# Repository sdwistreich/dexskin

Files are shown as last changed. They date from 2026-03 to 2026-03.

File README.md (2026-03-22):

# DexSkin (CoRL 2025)

DexSkin Demo

Suzannah Wistreich*, Baiyu Shi*, Stephen Tian*, Samuel Clarke, Michael Nath, Chengyi Xu, Zhenan Bao, Jiajun Wu  
Stanford University, UAB · CoRL 2025  

🔗 Project page: https://dex-skin.github.io

## 🎉 Open-Source Release: DexSkin — High-Coverage Conformable Robotic Skin for Contact-Rich Manipulation

We are excited to release **DexSkin**! 🎊  

DexSkin is a soft, high-resolution, conformable tactile sensing system designed for **contact-rich robotic manipulation**. It enables dense, localized sensing across complex surfaces and supports learning-based control in real-world settings.

---
## Getting Started

**This repository contains the full stack needed to:**

- **Fabricate the DexSkin sensor** → [hardware/README.md](hardware/README.md)  
- **Set up + interface with the hardware** → [firmware/README.md](firmware/README.md)  
- **Integrate DexSkin with learning pipelines** → [learning/README.md](learning/README.md)  

---

## Repository Overview

```
hardware/
  ├── finger/          # electrode design, finger assembly
  ├── fpcb/            # PCB interconnects
  ├── calibration/     # pneumatic calibration setup (STLs)
  └── readout_pcb/     # readout board Gerbers

firmware/    
  ├── dexskin_finger_firmware.bin       # ESP32 flashing binaries
  └── scripts/                          # readout and visualization scripts

learning/
  └── scripts/        # RL integration example
```
---

## BibTeX

If you found this open-source helpful, please consider citing:
```
@inproceedings{wistreich2025dexskin,
    title={DexSkin: High-Coverage Conformable Robotic Skin for Learning Contact-Rich Manipulation},
    author={Suzannah Wistreich and Baiyu Shi and Stephen Tian and Samuel Clarke and Michael Nath and Chengyi Xu and Zhenan Bao and Jiajun Wu},
    booktitle={Conference on Robot Learning (CoRL)},
    year={2025},
    eprint={2509.18830},
    archivePrefix={arXiv},
    primaryClass={cs.RO},
    url={https://arxiv.org/abs/2509.18830},
}
```

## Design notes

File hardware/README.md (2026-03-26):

# Hardware & Assembly Instructions

This folder contains DexSkin hardware assets for fabricating the sensor, ordering the PCBs, and reproducing the calibration setup described in the paper.

## Release Status

Currently available in this folder:

- Finger electrode SVG layout
- Flexible PCB manufacturing files for the sensor array interconnects
- Readout PCB Gerbers
- Calibration fixture STLs

In progress (target: mid-April 2026):

- Readout board BOM
- Calibration fabrication guide
- Assembly and ordering recommendations

## Folder Guide

### `finger/`

- `DexSkin_Electrode_design.svg`: Layout of top and bottom capacitive electrode layers for the finger design described in the paper
  - *For researchers interested in access to the stretchable cylindrical DexSkin form described in the paper or tactile arrays in other grid formats, please contact Baiyu Shi at the Bao Group (`baiyushi@stanford.edu`) regarding sample availability.*

### `fpcb/`

- `dexskin_5pin_row_interconnection.zip` and `dexskin_12pin_column_interconnection.zip`: flexible PCB interconnect files for the stretchable cylindrical DexSkin embodiment described in the paper.
- `5pin_row_fabrication_output.zip` and `12pin_column_fabrication_output.zip`: fabrication-ready Gerber packages for the 5 x 12 taxel flexible sensor layout for easy adoption.
- 5 x 12 taxel layout, mountable on flat or cylindrical grippers
- 2.5 mm x 2.5 mm square taxels
- 1.5 mm spacing between neighboring taxels

Special flex-PCB ordering notes:

- These fabrication-output Gerbers include a few layer specifications that should be communicated explicitly to the flex-PCB vendor during ordering
- **Mechanical Layer 1**: PCB outline
- **Top Overlay**: top EMI shielding film outline
- **Bottom Overlay**: bottom stiffener outline

### `readout_pcb/`

- `dexskin_readout_pcb_v1.1.zip`: Manufacturing files for the 4-layer readout board used to read both finger arrays simultaneously, prepared as a fabrication-ready Gerber archive

### `calibration/`

- `Final_Mold_Top.stl` 
- `Final_Mold_Bot.stl` 
- `Final_Mold_Supporting_Platform.stl` 
- `D20.8_Inner_Sleeve_TOP.stl`
- `D20.8_Inner_Sleeve_BOT.stl`
    - 3D-printable parts used to mold the Ecoflex and build airtight chambers for the 3-minute transfer calibration procedure described in the paper.

## Assembly Guide
Assembly overview:

DexSkin Demo

For a full walkthrough, please see the [assembly video](https://dex-skin.github.io/open_source.html#assembly-guide) on our project website!

**Materials**
- Two fabricated fPCB pieces
- Thin double-sided tape
- Nonconductive dielectric layer
- Sharp scalpel for trimming dielectric and tape
  
In our builds, we use a sandpaper-structured midlayer as the dielectric.

**Procedure**
1. **Prepare base layer**:
   
     Apply double-sided tape along the boundary of one fPCB piece.
2. **Attach dielectric**:

     Laminate the dielectric layer onto the second fPCB piece, trimming as needed.
3. **Align electrodes**:

     Carefully align the top and bottom electrode layers by matching the exposed copper taxels.
4. **Bond Assembly**:

     Press around the edges to ensure the double-sided tape bonds the two pieces together securely.

After assembly, verify the sensor by following the firmware instructions provided in [`../firmware/README.md`](../firmware/README.md). Then, run:
- [`../firmware/scripts/readout.py`](../firmware/scripts/readout.py)
- [`../firmware/scripts/visualize.py`](../firmware/scripts/visualize.py)

to verify that the sensor reads out correctly and view the real-time visualization:

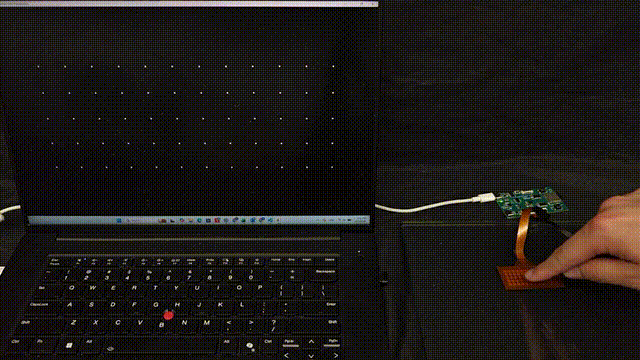
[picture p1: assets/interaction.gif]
DexSkin Demo


## Manufacturing Notes

- The ZIP archives in `fpcb/` and `readout_pcb/` are intended for direct submission to a PCB manufacturer.
- If your manufacturer asks for layer clarification on the flexible PCB files, you may use the layer notes above.

## Planned Additions

- Readout PCB BOM, including alternative parts where distributor availability changes
- Calibration fixture build notes
- Step-by-step assembly guidance

Last updated: March 26, 2026

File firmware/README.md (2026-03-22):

# DexSkin Interfacing Setup Guide

This guide explains:
- [DexSkin firmware setup](#firmware-setup)
- [Board readout and visualization scripts](#readout--visualization-setup)

Compatible with **Windows, macOS, and Linux**

---
## Firmware Setup

### 1. Install FTDI Drivers

If you haven’t worked with embedded systems before, you will need a driver to communicate with the onboard Serial USB. Please visit and install the USB serial drivers:

https://ftdichip.com/drivers/vcp-drivers/

- Select your OS and install
- **Linux:** typically already installed (check via Step #3)

---

### 2. Install Flashing Tool (esptool)

The esptool utility is a universal Python-based application used to communicate and flash in firmware with the ESP32 MCU series.

    pip install esptool

---

### 3. Identify Serial Port

Connect the board via USB-C.

If there are two ports, orient the board such that ESP32 is facing up, antenna is on the right, and the use **top-left port**.

You need to identify the specific port and its name assigned to the connected board:

**Windows**

Right-click the Start menu, select Device Manager, and expand Ports (COM & LPT). Look for USB Serial Port (`COMx`).

**macOS**

    ls /dev/cu.usbserial*

**Linux**

    ls /dev/ttyUSB*

---

### 4. Flash Firmware

Download the provided [`dexskin_finger_firmware.bin`](../firmware/dexskin_finger_firmware.bin). Navigate to the firmware directory and run:

    esptool --chip esp32s3 --port PORT --baud 460800 write_flash 0x0 dexskin_finger_firmware.bin

Replace `PORT` with your device found in Step #3.

**Example (macOS):**

    esptool --chip esp32s3 --port /dev/cu.usbserial-DP05L1VU --baud 460800 write_flash 0x0 dexskin_finger_firmware.bin

---

### 5. Troubleshooting

**Automatic Boot:**  
The board should enter flashing mode automatically once the flash command is executed.

**If “Failed to connect”:**
1. Hold **User/Boot** on the top right of the board.
2. Press + release **Reset** on the bottom right of the board.
3. Release **User/Boot** button before retrying flash command.
4. Retry flash command.

---

### 6. Completion

When the terminal displays

    Hard resetting via RTS pin…

the firmware update is complete.

You may need to press the **Reset** button once more to cleanly power cycle and boot up the system.

---

## Board Readout & Visualization Scripts

### Python Dependencies

We provide two Python scripts for interfacing and visualization DexSkin sensor readings.  
Tested with Python 3.10 (Python ≥ 3.8 supported).

**Required packages:**
- PyQt5 (5.15.11)
- pyqtgraph (0.13.7)
- pyserial (3.5)
- numpy (2.0.2)

**Quick Setup (conda example):**

    conda create -n dexskin_env python=3.10 -y
    conda activate dexskin_env
    pip install PyQt5==5.15.11 pyqtgraph==0.13.7 pyserial==3.5 numpy==2.0.2

---

### Script Overview

The software architecture is split into two independent processes that communicate via shared memory. This allows the readout script to run at high priority for data logging, while the visualization script consumes data for display without slowing down sensor sampling.

- **[`./scripts/readout.py`](./scripts/readout.py)**: Handles serial communication, packet decoding, and baseline normalization. **Always run this script first**, it must be running for the visualization or any other application to access sensor data.

- **[`./scripts/visualize.py`](./scripts/visualize.py)**: Provides a real-time visualization of tactile data for both the left and right fingers. Each taxel is displayed as a white dot, with dot size proportional to the raw sensor values (sampled pressure / force magnitude). If the script is running correctly, the visualization will look like:

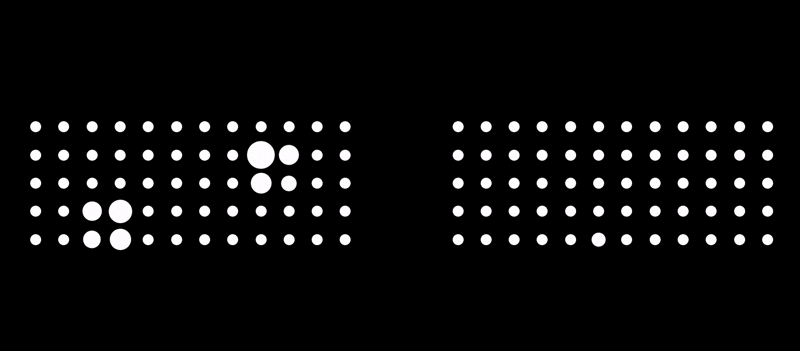
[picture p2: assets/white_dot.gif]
DexSkin Demo


---

### Developer Guide: Interfacing with Shared Memory

The DexSkin system exposes its real-time data buffer to the operating system’s shared memory. This allows developers to write their own scripts (e.g., for Machine Learning inference, ROS robot control, or custom logging) without modifying the core driver.

Any Python script running on the same machine can attach to the shared memory block as a client:

    SHM_NAME = 'dexskin_memory'
    NUM_TAXELS = 120

    try:
        self.shm = shm.SharedMemory(name=SHM_NAME)
        self.frame_buffer = np.ndarray((NUM_TAXELS,), dtype=np.float32, buffer=self.shm.buf)
        print(f"Attached to shared memory: {SHM_NAME}")
    except FileNotFoundError:
        print(f"ERROR: Shared memory block '{SHM_NAME}' not found.")
        print("Please ensure the data providing script is running.")
        sys.exit(1)

Then in other function calls, use:

    self.frame_buffer.copy()

to access latest data.

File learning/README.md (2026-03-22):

# DexSkin Learning Guide

This guide gives a brief overview of data collection and base policy training with DexSkin. We also provide several sample scripts for RL fine-tuning with DexSkin.

---

## Data Collection

We collect real-world demonstrations using a teleoperated Franka robot setup equipped with DexSkin sensors.

Each demonstration consists of:
- Robot observations (e.g., proprioception, optional vision via wrist camera)
- DexSkin tactile readings
- Corresponding action trajectories

These demonstrations are used to train policies via imitation learning. In our setup, ~50 human demonstrations per task are sufficient to learn a reasonable base policy.

---

## Base Policy Training

We train a base manipulation policy using a standard **diffusion policy** formulation, though any imitation-learning framework will do.

---

## RL Fine-Tuning with DexSkin

We provide a small set of **example residual RL scripts** to illustrate how DexSkin can be used in real-world, online learning settings. These scripts are provided as a helpful reference implementation. In particular, reward functions, force thresholds, termination conditions, etc. should be adapted to one's own target task and hardware setup.

### Script Overview

- **[`./scripts/franka_env_with_policy.py`](./scripts/franka_env_with_policy.py)**: Defines a Gym-compatible Franka environment that combines a pretrained diffusion policy with a residual controller. The residual action modifies the base policy's gripper action online, where DexSkin signals are used to compute force-threshold rewards together with an action-magnitude penalty.

- **[`./scripts/residual_inference_train_env.py`](./scripts/residual_inference_train_env.py)**: Constructs a `FrankaEnvWithPolicy` environment (from `franka_env_with_policy.py`) and runs Franka rollouts with the base policy plus a residual controller, which is one of:
  - (default) a learned residual policy
  - `--base_policy_only`: the base policy only
  - `--random_residual`: a random residual baseline  

If neither `--base_policy_only` nor `--random_residual` is set, this script can also continue updating the learned residual policy online.

- **[`./scripts/residual_train.py`](./scripts/residual_train.py)**: Trains a residual SAC policy online on the Franka robot. This script loads the pretrained base policy, constructs the DexSkin-enabled `FrankaEnvWithPolicy` environment, performs online rollouts, updates the residual policy, and periodically saves checkpoints.

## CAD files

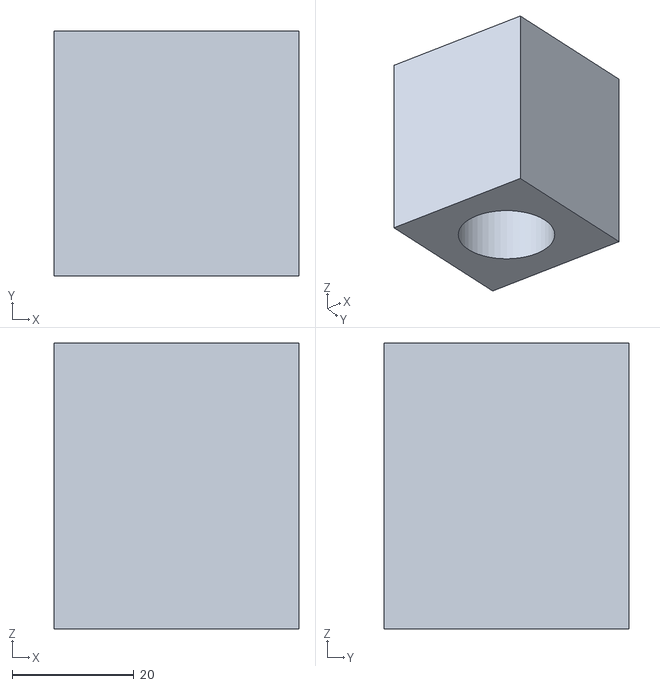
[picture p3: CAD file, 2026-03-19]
hardware/calibration/D20.8_Inner_Sleeve_TOP.stl
40.2 x 40.2 x 47.0

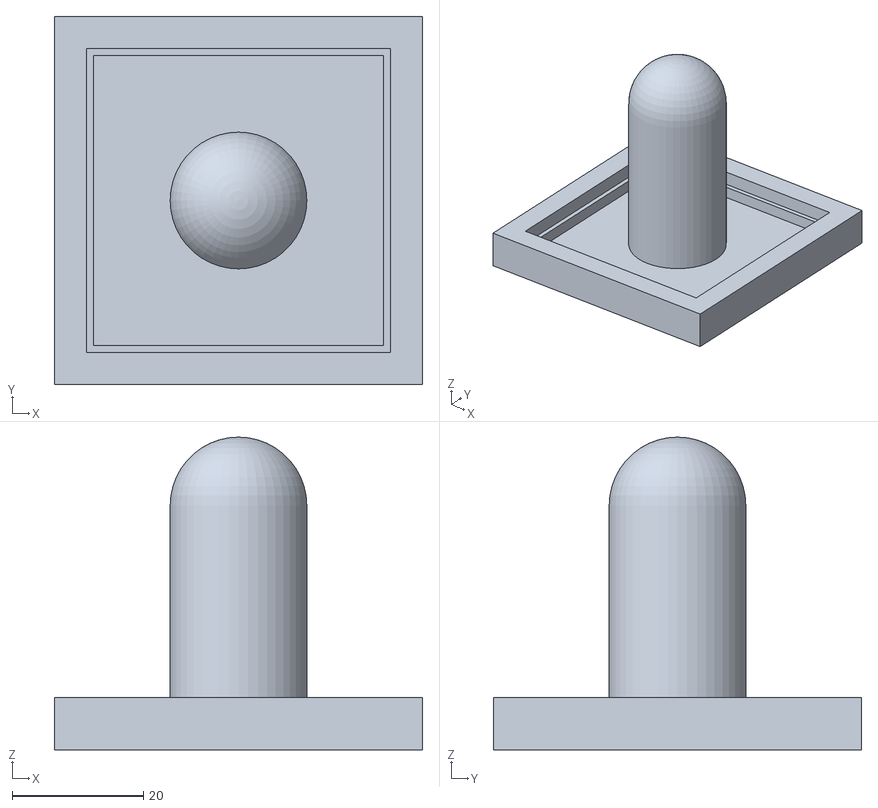
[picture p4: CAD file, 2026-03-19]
hardware/calibration/Final_Mold_Bot.stl
56.0 x 56.0 x 47.6

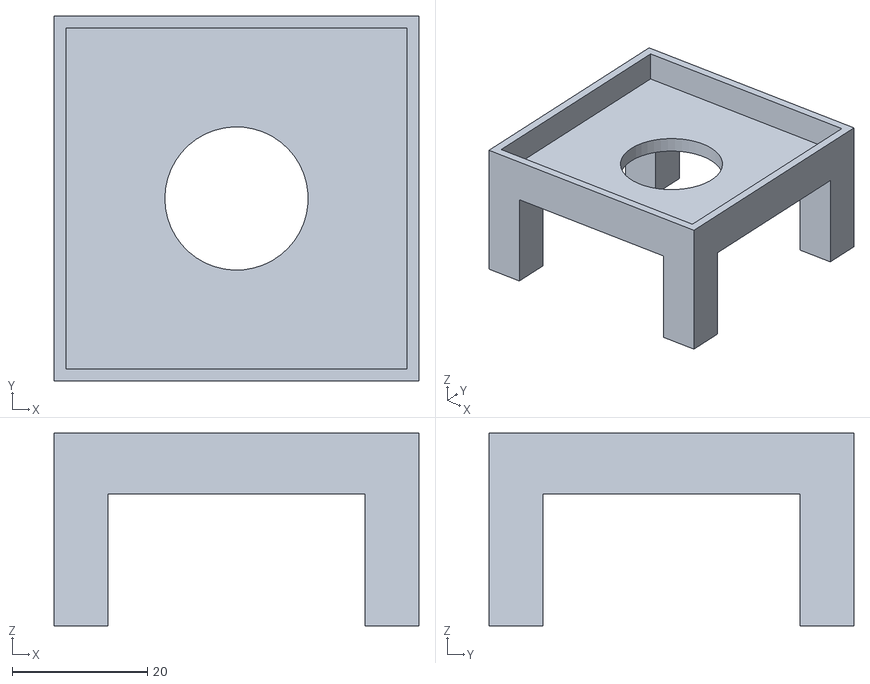
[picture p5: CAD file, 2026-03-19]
hardware/calibration/Final_Mold_Supporting_Platform.stl
54.0 x 54.0 x 28.5

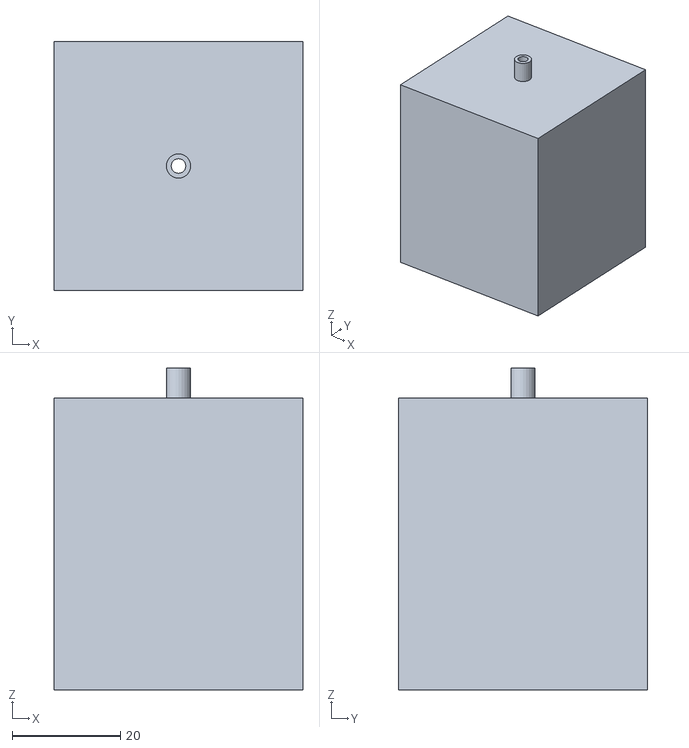
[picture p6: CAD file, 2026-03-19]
hardware/calibration/Final_Mold_Top.stl
46.0 x 46.0 x 59.5

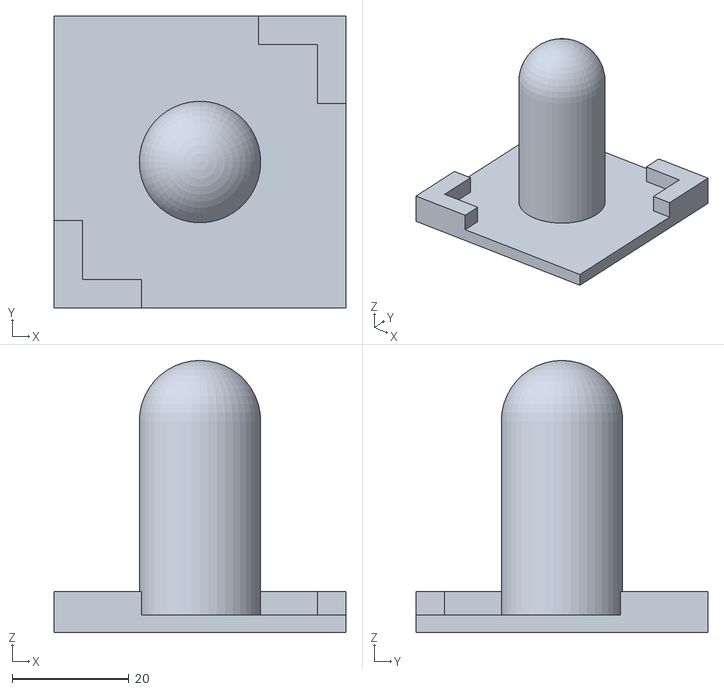
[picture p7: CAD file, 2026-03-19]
hardware/calibration/D20.8_Inner_Sleeve_BOT.stl
50.0 x 50.0 x 46.6

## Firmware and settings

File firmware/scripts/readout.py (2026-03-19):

# File name: readout.py
# Author: Baiyu Shi
# Date created: Jan.2025
# Version: v1.3

import serial
import time
import numpy as np
from multiprocessing.shared_memory import SharedMemory
import threading
from serial import SerialException

#the main parameters to change.
PORT = 'COM3'      
BAUDRATE = 460800         #specify the baud rate, default to 460800 with the provided firmware.
NUM_TAXELS = 120            
numRow = 10
numCol = 12
NUM_TAXELS = numRow * numCol       
BASELINE_SAMPLE_NUM = 30      # Number of frames to be averaged for baselines.
FLUSH_FRAME_COUNT = 50        # Number of initial frames to flush to stabilize readouts.
TIMEOUT = 1            
SHM_NAME = 'dexskin_memory' # Shared memory block name

ITEMSIZE = np.dtype(np.float32).itemsize
BUFSIZE = NUM_TAXELS * ITEMSIZE
try:
    shm = SharedMemory(name=SHM_NAME, create=True, size=BUFSIZE)
    print(f"Created New Shared Memory")
except FileExistsError:
    shm = SharedMemory(name=SHM_NAME, create=False)
    print(f"Attached to Existing Memory '{SHM_NAME}'")
shared_frame = np.ndarray((NUM_TAXELS,), dtype=np.float32, buffer=shm.buf)

class MCUController1DShared:
    def __init__(self):
        self.port = PORT
        self.baudrate = BAUDRATE
        self.timeout = TIMEOUT
        self.serial = None

        #baseline and std instantiation.
        self.CurrentFrame = np.zeros(NUM_TAXELS, dtype=np.float32)
        self.baseline = np.zeros(NUM_TAXELS, dtype=np.float32)
        self.std = np.ones(NUM_TAXELS, dtype=np.int32)

        #for calculating FPS.
        self._frame_count = 0
        self._last_fps_time = time.time()
        self.fps = 0.0
        self.running = False

        try:
            self.connect()
            self.init_flush()
            self.start_periodic_task()
        except SerialException as e:
            print(f"SerialException: {e}")

    def connect(self):
        """Open serial port."""
        self.serial = serial.Serial(self.port, self.baudrate, timeout=self.timeout)
        print(f"Serial connected on {self.port} at {self.baudrate}")

    def init_flush(self):
        """
        Discard FLUSH_FRAME_COUNT number of initial frames, then collect
        BASELINE_SAMPLE_NUM frames to compute per-taxel baseline and std.
        """
        flushed = 0
        while flushed < FLUSH_FRAME_COUNT:
            f = self.read_frame(initial=True)
            if f is not None:
                flushed += 1

        frames = []
        while len(frames) < BASELINE_SAMPLE_NUM:
            f = self.read_frame(initial=True)
            if f is not None:
                frames.append(f)

        arr = np.stack(frames, axis=0)
        # compute mean baseline
        self.baseline = np.mean(arr, axis=0)
        var = np.mean((arr - self.baseline)**2, axis=0)
        float_std = np.sqrt(var)
        self.std = float_std.astype(np.int32)
        self.std[self.std < 1] = 1

        print("Baseline computed:", self.baseline)
        print("Std deviation, expected to be below 1:", self.std)

    def read_frame(self, initial=False):
        if self.serial is None:
            raise Exception("Serial not connected.")

        try:
            line = self.serial.readline()
            raw_values = [
                int(val) for val in line.decode('utf-8').rstrip().split(',')
                if val != ''
            ]

            if len(raw_values) != numRow * numCol:
                return None

            frame = np.array(raw_values, dtype=np.int32)
            if frame.size != NUM_TAXELS:
                return None

            if initial:
                return frame

            # normalize and push to shared memory
            self.CurrentFrame = (frame.astype(np.float32) - self.baseline) / self.baseline
            shared_frame[:] = self.CurrentFrame

            self._frame_count += 1
            self._update_fps()
            return None
        
        
        except Exception as e:
            print(f"Error retrieving frame: {e}")
            return None


    def _update_fps(self):
        now = time.time()
        delta = now - self._last_fps_time
        if delta >= 1.0:
            self.fps = self._frame_count / delta
            self._frame_count = 0
            self._last_fps_time = now

    def get_fps(self):
        return self.fps

    def periodic_task(self):
        self.running = True
        interval = 1 / 120
        while self.running:
            self.read_frame(initial=False)
            time.sleep(interval)

    def start_periodic_task(self):
        t = threading.Thread(target=self.periodic_task, daemon=True)
        t.start()
        self.thread = t
        print(f"Started reader thread")

    def stop(self):
        """
        Stop the thread and clean up shared memory.
        Please call this before exiting.
        """
        self.running = False
        if hasattr(self, 'thread'):
            self.thread.join()
        shm.close()
        try:
            shm.unlink()
        except FileNotFoundError:
            pass
        print("Stopped and cleaned up shared memory.")

    def get_frame(self):
        return self.CurrentFrame

if __name__ == '__main__':
    ctrl = MCUController1DShared()
    try:
        while True:
            print(f"FPS: {ctrl.get_fps():.1f}")
            time.sleep(0.5)
    except KeyboardInterrupt:
        #use Keyboard interrupts to end the thread and safely unlink the memory.
        ctrl.stop()

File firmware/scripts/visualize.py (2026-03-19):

# File name: visualize.py
# Author: Baiyu Shi
# Date last modified: 01/09/2025

import numpy as np
import pyqtgraph as pg
from PyQt5 import QtCore, QtGui, QtWidgets
import sys
import multiprocessing.shared_memory as shm

#parameters.
SHM_NAME = 'dexskin_memory'  # Shared memory block name
NUM_TAXELS = 120             # Total number of taxels (5*12*2)
timerDelay = 33             #33ms updates for 30Hz update.

#parameters defining visualization dot layout.
finger_rows = 5
finger_cols = 12
gap = 4.0

positions = []

#visualization settings
min_val, max_val = 0.05, 1.0
min_dot_size = 10
max_dot_size = 150

# Right finger (positive x) on the right of GUI
for r in range(finger_rows):
    for c in range(finger_cols):
        # x starts from gap/2, y is centered vertically around 0
        x = c + gap / 2.0
        y = r - (finger_rows - 1) / 2.0
        positions.append([x, y])

# Left finger (negative x) on the left of GUI.
for r in range(finger_rows):
    for c in range(finger_cols):
        # x starts from -gap/2 and goes left, creating a mirror image
        x = -(c + gap / 2.0)
        y = r - (finger_rows - 1) / 2.0
        positions.append([x, y])

positions = np.array(positions)
assert len(positions) == NUM_TAXELS, "Position array length must match NUM_TAXELS"


class DualFingerVisualization(QtWidgets.QMainWindow):
    def __init__(self):
        super().__init__()
        self.setWindowTitle('DexSkin Tactile Data Visualization')
        self.resize(800, 600)

        try:
            self.shm = shm.SharedMemory(name=SHM_NAME)
            self.frame_buffer = np.ndarray(
                (NUM_TAXELS,), dtype=np.float32, buffer=self.shm.buf
            )
            print(f"Attached to shared memory: {SHM_NAME}")
        except FileNotFoundError:
            print(f"ERROR: Shared memory block '{SHM_NAME}' not found.")
            print("Please ensure the data providing script is running.")
            sys.exit(1)

        graphicswidget = pg.GraphicsLayoutWidget()
        self.setCentralWidget(graphicswidget)
        
        view = graphicswidget.addViewBox()
        view.setAspectLocked(True)
        self.scatter = pg.ScatterPlotItem()
        view.addItem(self.scatter)

        min_x, min_y = positions.min(axis=0)
        max_x, max_y = positions.max(axis=0)

        view.invertY(True)

        padding = 1.0
        view.setRange(
            QtCore.QRectF(
                min_x - padding,
                min_y - padding,
                (max_x - min_x) + 2 * padding,
                (max_y - min_y) + 2 * padding
            )
        )
        
        self.timer = QtCore.QTimer()
        self.timer.timeout.connect(self.update_scatter)
        self.timer.start(timerDelay)

    def update_scatter(self):
        #getting the data from the shared frame buffer.
        flat_frame = self.frame_buffer.copy()

        clipped = np.clip(flat_frame, min_val, max_val)
        normalized = (clipped - min_val) / (max_val - min_val)
        sizes = min_dot_size + normalized * (max_dot_size - min_dot_size)

        self.scatter.setData(
            pos=positions,
            size=sizes,
            brush=pg.mkBrush(255, 255, 255),  
            pen=pg.mkPen(None)             
        )

    def closeEvent(self, event):
        """Clean up shared memory on window close."""
        print("Closing shared memory attachment.")
        self.shm.close()
        event.accept()


if __name__ == '__main__':
    app = QtWidgets.QApplication(sys.argv)
    win = DualFingerVisualization()
    win.show()
    sys.exit(app.exec_())

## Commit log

2026-03-22 vis sample
2026-03-25 .
    Updated descriptions for flexible PCB files and layer notes.
2026-03-25 small edits
    Updated assembly instructions with detailed materials and procedure steps.
